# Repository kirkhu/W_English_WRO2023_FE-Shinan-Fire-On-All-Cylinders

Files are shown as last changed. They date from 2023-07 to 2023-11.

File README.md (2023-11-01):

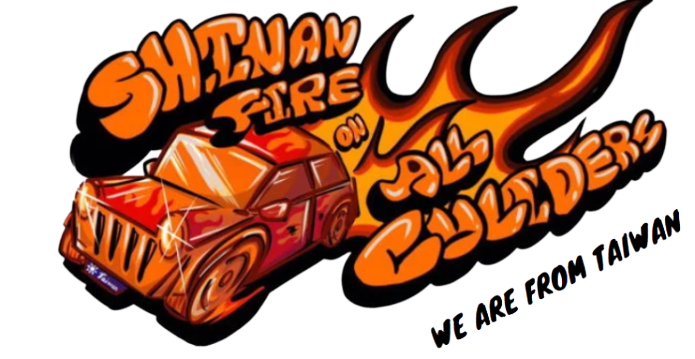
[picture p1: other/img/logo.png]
logo
 

- This is the official GitHub repository for the WRO TAIWAN team "__Shinan Fire On All Cylinders.__" All code, documentation, and files are located here.
- Here you can find the links to the technical report content and setup instructions, organized separately for learners and judges, for easy access during either learning or assessment. 
- In this technical document, the directory will be established based on the scoring criteria, and the directory headings will be hyperlinked for easy access for judges or learners to navigate to the key content of the technical document, facilitating quick assessment.  
    #### [For Learners](https://github.com/kirkhu/WRO2023_FE-Shinan-Fire-On-All-Cylinders/blob/main/learners_contents.md)
## Rubric for Judging Engineering Documentation 
- ###  ${{\color{red} Hardware Overview }} $ 
  #### 1. Mobility Management
    * [1-1 Vehicle 2D/3D Models in CAD](https://github.com/kirkhu/WRO2023_FE-Shinan-Fire-On-All-Cylinders/blob/main/models/Vehicle_2D_3D/README.md)
    * [1-2 Motor Selection](https://github.com/kirkhu/WRO2023_FE-Shinan-Fire-On-All-Cylinders/blob/main/schemes/Motor/README.md)
    * [1-3 Vehicle Chassis Design](https://github.com/kirkhu/WRO2023_FE-Shinan-Fire-On-All-Cylinders/blob/main/schemes/Vehicle_Chassis_Design/README.md)

  #### 2. Power and Sense Management
    - __Vehicle Design__
      - [2-1-1 BOM Parts List](https://github.com/kirkhu/WRO2023_FE-Shinan-Fire-On-All-Cylinders/blob/main/schemes/Parts_List#readme)
      - [2-1-2 Circuit Design](https://github.com/kirkhu/WRO2023_FE-Shinan-Fire-On-All-Cylinders/blob/main/models/Circuit_Design/README.md)
      - [2-1-3 Hardware Fool-Proof Design](https://github.com/kirkhu/WRO2023_FE-Shinan-Fire-On-All-Cylinders/blob/main/schemes/fool-proof-design/README.md) 
      - [2-1-4 Assembly Instructions & Wiring Diagrams](https://github.com/kirkhu/WRO2023_FE-Shinan-Fire-On-All-Cylinders/blob/main/schemes/Assembly_Instructions/README.md)    
      
    - __Power Management__
      - [2-2-1 Power Supply System](https://github.com/kirkhu/WRO2023_FE-Shinan-Fire-On-All-Cylinders/blob/main/schemes/Power_supply_system/README.md) 
      - [2-2-2 Li-Polymer Battery Low Voltage Alarm and Charging Equipment](https://github.com/kirkhu/WRO2023_FE-Shinan-Fire-On-All-Cylinders/blob/main/schemes/Li-Polymer_Battery/README.md)  
   
    - __Controller Selection__
      - [2-3-1 Controller Comparison](https://github.com/kirkhu/WRO2023_FE-Shinan-Fire-On-All-Cylinders/tree/main/other/Controller_Choosing)
    - __Sense Management__
      - [2-4-1 Color Sensor Introduction](https://github.com/kirkhu/WRO2023_FE-Shinan-Fire-On-All-Cylinders/blob/main/schemes/color_sensor/README.md)
      - [2-4-2 Lidar Selection](https://github.com/kirkhu/WRO2023_FE-Shinan-Fire-On-All-Cylinders/blob/main/schemes/Lidar/README.md)
      - [2-4-3 Camera Selection](https://github.com/kirkhu/WRO2023_FE-Shinan-Fire-On-All-Cylinders/blob/main/schemes/Camera/README.md)
  
- ### ${{\color{red} Software Overview }} $ 
  #### 3. Obstacle Management
    - [3-1 OpenCV Introduction](https://github.com/kirkhu/WRO2023_FE-Shinan-Fire-On-All-Cylinders/blob/main/other/OpenCV/README.md)
    - [3-2 ROS Introduction](https://github.com/kirkhu/WRO2023_FE-Shinan-Fire-On-All-Cylinders/blob/main/other/ROS)
    - [3-3 Software Platform Construction](https://github.com/kirkhu/WRO2023_FE-Shinan-Fire-On-All-Cylinders/blob/main/src/System_Platform_Software/README.md)
    - __Image Processing and Steering__
      - [3-4-1 Image Processing](https://github.com/kirkhu/WRO2023_FE-Shinan-Fire-On-All-Cylinders/blob/main/src/Image_Processing_and_Steering/Image_Processing/README.md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)  
      - [3-4-2 Steering Overview](https://github.com/kirkhu/WRO2023_FE-Shinan-Fire-On-All-Cylinders/blob/main/src/Image_Processing_and_Steering/Steering_overview/README.md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) 
    - __Programming__
      - [3-5-1 Open Challenge Code Overview](https://github.com/kirkhu/WRO2023_FE-Shinan-Fire-On-All-Cylinders/blob/main/src/Programming/Open_Challenge)
      - [3-5-2 Obstacle Challenge Code Overview](https://github.com/kirkhu/WRO2023_FE-Shinan-Fire-On-All-Cylinders/blob/main/src/Programming/Obstacle_Challenge)
      - [3-5-3 Distinctive Pseudo Code](https://github.com/kirkhu/WRO2023_FE-Shinan-Fire-On-All-Cylinders/blob/main/src/Distinctive_Pseudo_Code/README.md)
- ### ${{\color{red} Other}} $
  #### 4. Pictures – Team and Vehicle
    - [4-1 Team Members Introduction](https://github.com/kirkhu/WRO2023_FE-Shinan-Fire-On-All-Cylinders/blob/main/t-photos/README.md) 
    - [4-2 Vehicle Photos](https://github.com/kirkhu/WRO2023_FE-Shinan-Fire-On-All-Cylinders/tree/main/v-photos)  
  #### 5. Performance Videos
    - [5-1 Open Challenge](https://github.com/kirkhu/WRO2023_FE-Shinan-Fire-On-All-Cylinders/blob/main/video/Open_Challenge/video.md)
    - [5-2 Obstacle Challenge](https://github.com/kirkhu/WRO2023_FE-Shinan-Fire-On-All-Cylinders/blob/main/video/Obstacle_Challenge/video.md)
    - [5-3 Self-Driving Car Design Process Video](https://github.com/kirkhu/WRO2023_FE-Shinan-Fire-On-All-Cylinders/blob/main/video/ALL_video/video.md)
  #### 6. GitHub Utilization
    - [6-1 GitHub Edit(VScode Edit/GIT)](https://github.com/kirkhu/WRO2023_FE-Shinan-Fire-On-All-Cylinders/blob/main/src/GitHub_Edit/README.md)
    - [6-2 GitHub Web Editing Languages](https://github.com/kirkhu/WRO2023_FE-Shinan-Fire-On-All-Cylinders/blob/main/src/GitHub_Languages/README.md)  
  #### 7. Engineering Factor  
    - [7-1 Work Diary](https://github.com/kirkhu/WRO2023_FE-Shinan-Fire-On-All-Cylinders/blob/main/other/work_diary/README.md)
- ### ${{\color{red} CompetitionSchedule}} $  
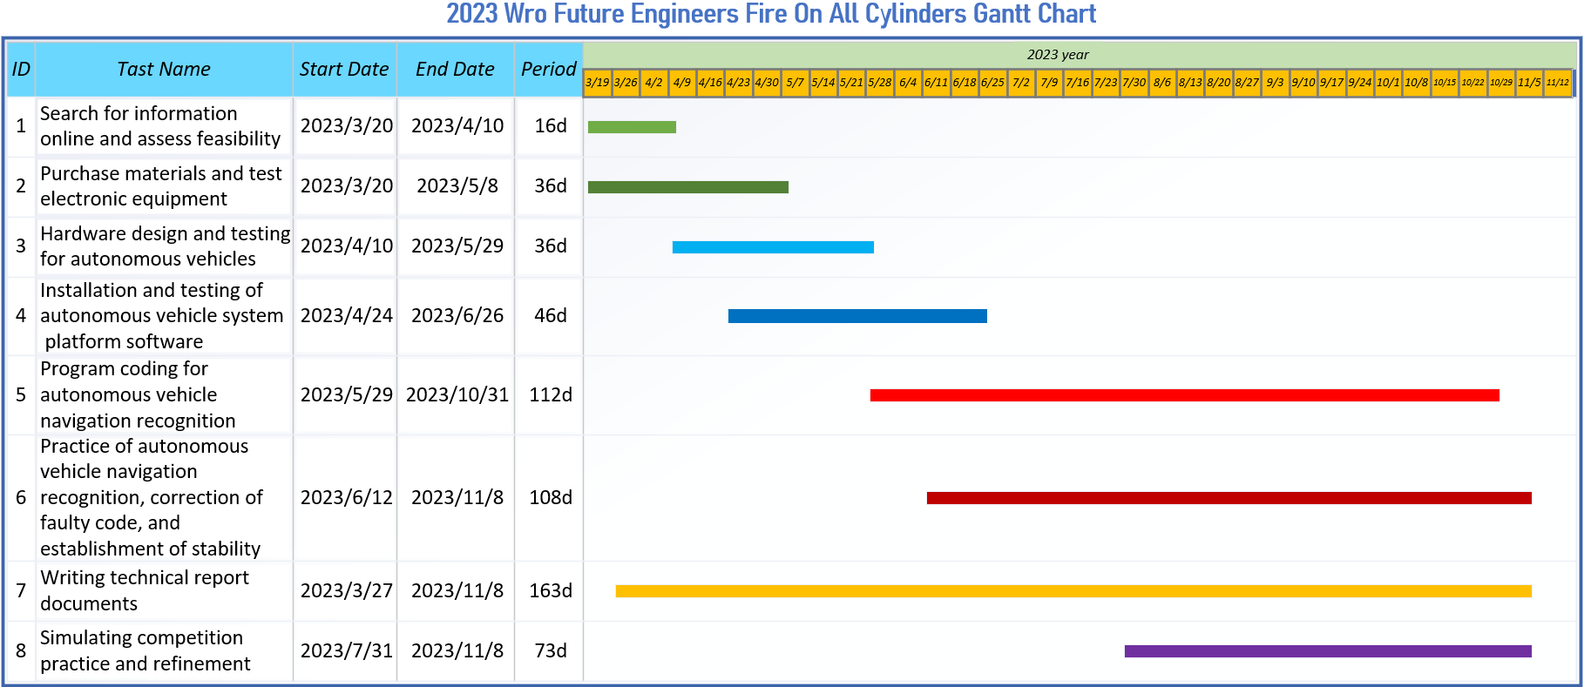
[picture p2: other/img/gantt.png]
Competition Schedule Gantt
#

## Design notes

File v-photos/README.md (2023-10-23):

<div align="center">logo</div>

- ## Vehicle's photos
<div align="center">
<table>
  <tr align="center">
    <th>Top view</th>
    <th>Bottom view </th>

  </tr>
    <tr align="center">
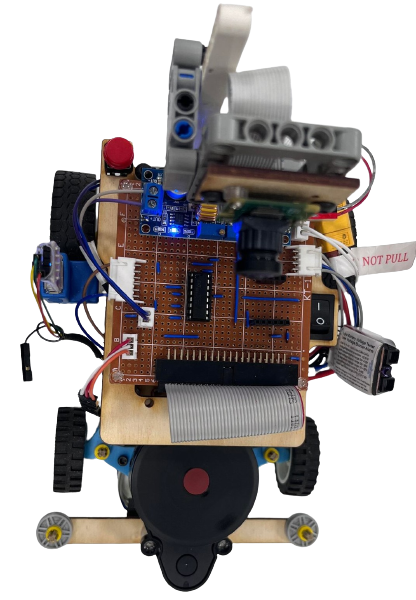
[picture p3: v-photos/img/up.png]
Top view
    <td> </td>
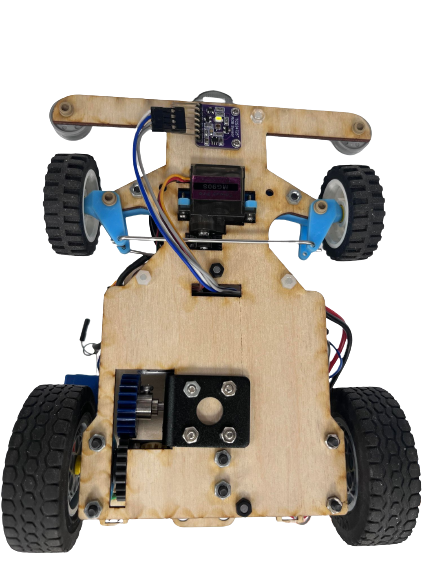
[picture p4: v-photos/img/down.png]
Bottom view
    <td></td>
  </tr>
    <tr align="center">
    <th> Front view</th>
    <th> Rear view </th>
  </tr>
    </tr>
    <tr align="center">
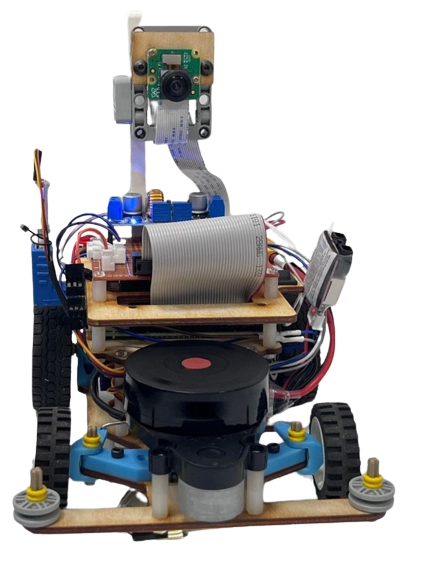
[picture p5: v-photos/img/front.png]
Front_view
    <td></td>
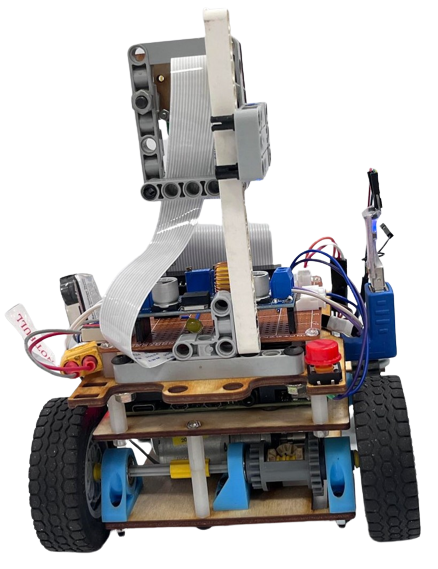
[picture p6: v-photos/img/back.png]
Rear_view
    <td></td>
  </tr>
    <tr align="center">
    <th> Left view</th>
    <th> Right view</th>
  </tr>
    </tr>
    <tr align="center">
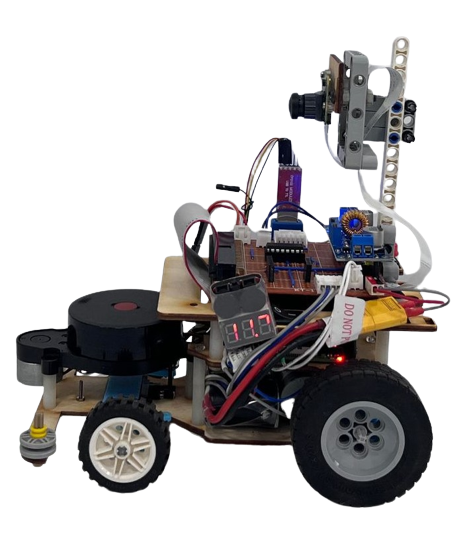
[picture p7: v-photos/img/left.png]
Left_view
    <td></td>
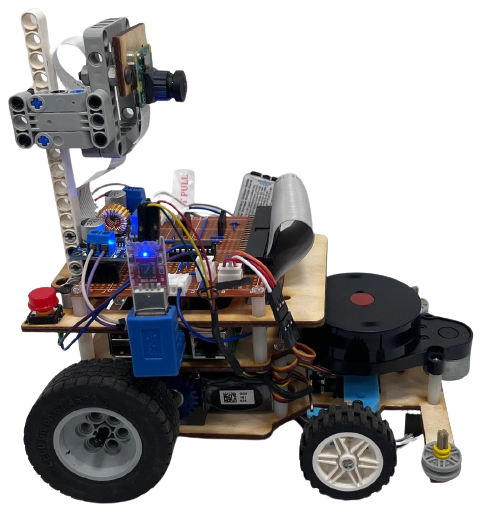
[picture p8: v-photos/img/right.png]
Right_view
    <td></td>
  </tr>
</table>
</div> 

- ## Mechanical Structure 
<div align="center">
<table>
  <tr align="center">
      <th>Overall Mechanical Structure Top View</th>
      <th>Middle-Level Mechanical Structure Top View</th>
      <th>Vehicle Chassis Top Views</th>
      <th>Vehicle Chassis Bottom View</th>
  </tr>
  <tr align="center">
     <td>Overall Mechanical Structure Top View      </td>
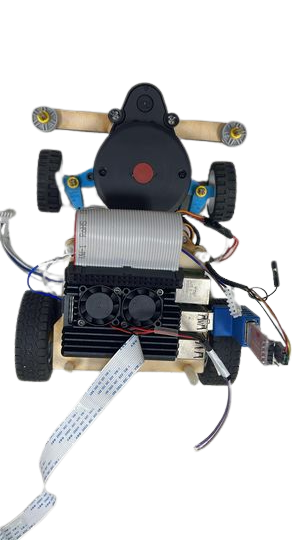
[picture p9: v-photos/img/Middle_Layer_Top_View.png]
Middle-Level Mechanical Structure Top View
     <td></td>
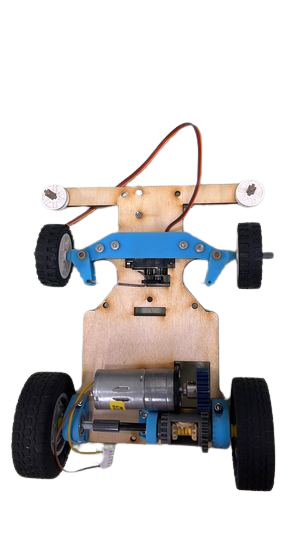
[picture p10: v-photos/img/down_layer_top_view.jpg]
Vehicle Chassis Top View
     <td></td>
     <td>BVehicle Chassis Bottom View</td>
  </tr>
</table>
</div>

- ### Circuit Board
<div align="center">
<table>
  <tr align="center">
      <th>Circuit Board of Top View</th>
      <th>Circuit Board of Bottom View</th>
  </tr>
  <tr align="center">
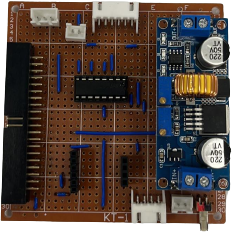
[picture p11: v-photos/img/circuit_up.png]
     <td>  </td>
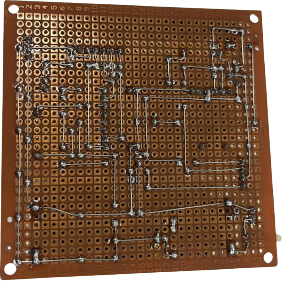
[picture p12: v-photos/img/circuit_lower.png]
     <td></td>
  </tr>
</table>
</div>

# <div align="center">HOME[Return Home](../)</div>

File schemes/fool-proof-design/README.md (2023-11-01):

<div align="center">logo</div>

## <div align="center">Hardware Fool-Proof Design</div>

- In the process of hardware design, there have been several cases of damage to Raspberry Pi controllers or ICs due to incorrect power connections or data cable insertion. To avoid this problem, we adopted a solution of using male and female sockets for power supply and data transmission. Through male and female sockets, the correct wiring is ensured, effectively avoiding the risk of Raspberry Pi or IC burning. This design improvement has increased the stability of the hardware system, improved the overall reliability and service life of the product.  
- In the process of hardware design, we initially used breadboards to connect circuits, but unfortunately encountered some cases of burning or poor contact, which led to abnormal function operation or potential problems that were difficult to find. To improve this situation, we decided to use soldering to fix the circuit on a PCB. This change has significantly reduced the risk of burning or poor contact, while ensuring a stable and reliable connection. Through this improvement, we have successfully improved the overall reliability of the hardware system and ensured the normal operation of the function.

<div align="center">

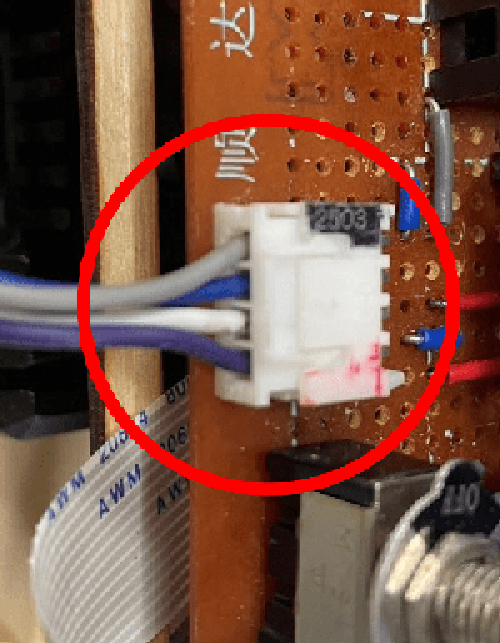
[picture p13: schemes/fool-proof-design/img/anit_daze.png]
Socket
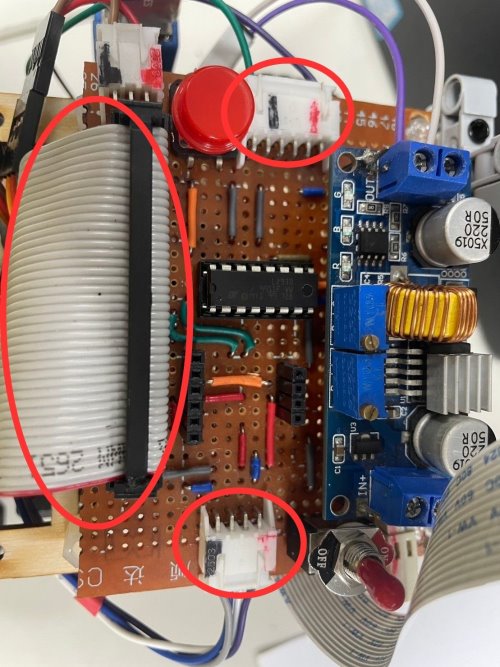
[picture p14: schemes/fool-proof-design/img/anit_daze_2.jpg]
Circuit Board
|   | |
|:----|:----:|
</div>
  
# <div align="center">HOME[Return Home](../../)</div>

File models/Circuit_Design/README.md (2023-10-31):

<div align="center">logo</div>

## <div align="center">Circuit Design </div>

 - In the design of self-driving car circuits, we used the Fritzing circuit software to draw circuit diagrams according to the functions required by self-driving cars. This method allows construction workers to follow the drawings and reduce errors.
 - The circuit board for the self-driving car is not a finished product that we purchased. Instead, we soldered it ourselves using a phenolic universal board, according to the circuit diagram we designed in advance.
 - Power and signal are two essential parts of self-driving car circuits. Power provides electricity to the circuit, while signal transmits data. Designing socket methods around the circuit board can facilitate the connection of sensors or batteries, which can improve the flexibility and scalability of the circuit.
   
 - #### Circuit Board
<div align="center">
<table>
  <tr align="center">
      <th> Circuit Board Top View</th><th>Circuit Board Button View</th>
  </tr>
  <tr align="center">
     <td> circuit_up </td><td></td>
  </tr>
</table>
</div>

- ### Circuit Schematic Drawing
<div align="center">
<table>
  <tr align="center">
      <th>Circuit Diagram</th><th>PCB Layouts</th><th>Circuit Schematic</th>
  </tr>
  <tr align="center">
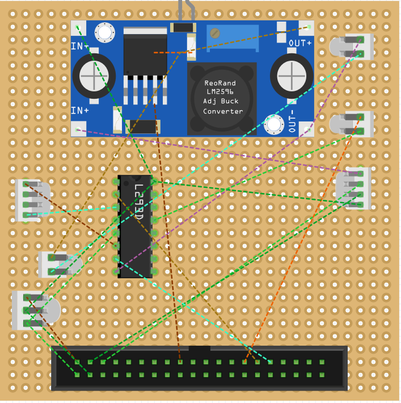
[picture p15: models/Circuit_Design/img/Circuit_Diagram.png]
Circuit Diagram
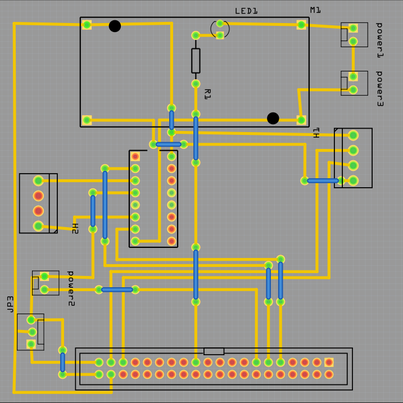
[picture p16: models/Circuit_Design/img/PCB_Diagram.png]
PCB Layouts
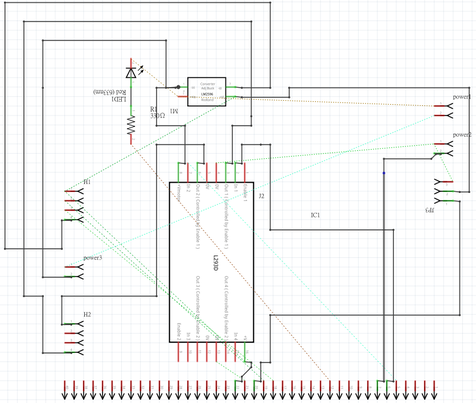
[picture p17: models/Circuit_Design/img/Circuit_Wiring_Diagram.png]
Circuit Schematic
     <td></td><td></td><td></td>
  </tr>
</table>
</div>

- ### Fritzing Introduction
  - Fritzing is a free and open-source electronic design automation (EDA) software. It provides a graphical user interface (GUI) for designing electronic circuits and circuit boards. Fritzing also includes a breadboard simulator, which allows users to test their circuits before building them.  
  - Fritzing is a popular choice for hobbyists and beginners, as it is easy to use and does not require any prior knowledge of electronics. It is also used by professional engineers for prototyping and designing electronic circuits.
  - Fritzing has a number of features that make it a powerful tool for electronic design, including:  
    - A large library of electronic components, including resistors, capacitors, transistors, and integrated circuits (ICs).  
    - A breadboard simulator that allows users to test circuits before building them.  
    - A PCB (printed circuit board) designer that allows users to create custom circuit boards.   
    - A schematic editor that allows users to create circuit diagrams.
  - In general, Fritzing is a very useful tool for a variety of electronic design applications. It is a good choice for hobbyists and beginners because it is easy to use and powerful. It is also a good choice for professional engineers because it has a wide range of features.
  - The circuit diagrams created for this competition are all designed using Fritzing.
  - Software link：[Fritzing](https://fritzing.org/)  
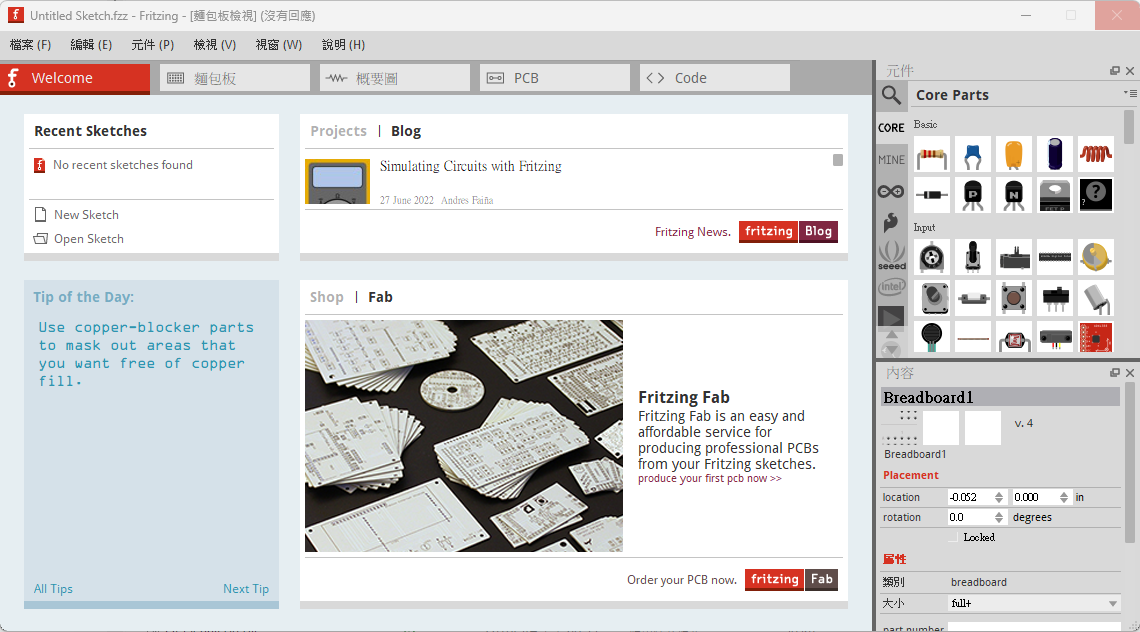
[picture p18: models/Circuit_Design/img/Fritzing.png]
Fritzing
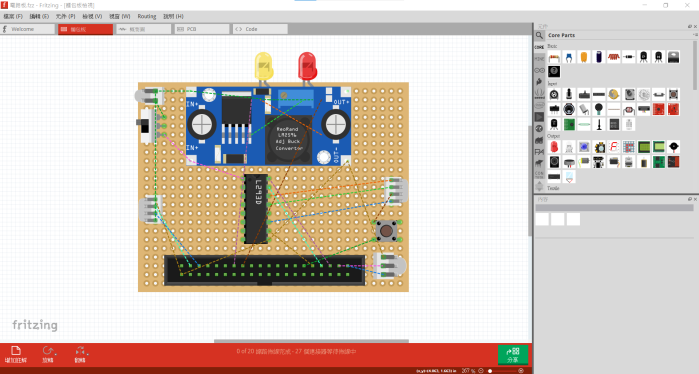
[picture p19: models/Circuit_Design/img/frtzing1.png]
  

# <div align="center">HOME[Return Home](../../)</div>

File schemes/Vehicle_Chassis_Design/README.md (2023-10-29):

<div align="center">logo</div>

## <div align="center">Vehicle Chassis Design Process</div> 

- ### Vehicle Chassis Design
  - The vehicle chassis used in this competition is self-designed and developed.
  - We applied Ackermann Steering Geometry to the vehicle chassis mechanism to facilitate obstacle avoidance and U-turns.
  - The following table shows the 3D models and finished products of the vehicle chassis.

    |3D Vehicle Chassis Design| Vehicle Chassis Top View | Vehicle Chassis Bottom View|
    |:----:|:----:|:----:|
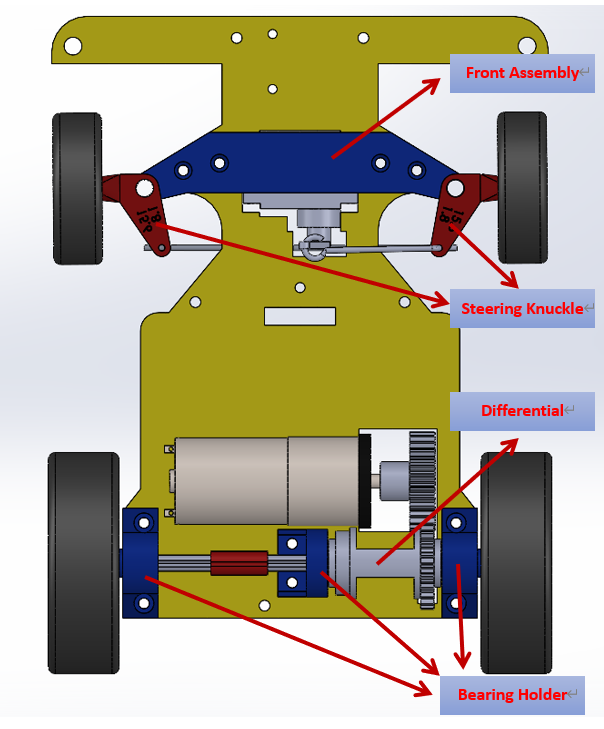
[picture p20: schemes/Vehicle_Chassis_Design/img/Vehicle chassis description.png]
vehicle_chassis_design_3D
    ||up_view|down_view|

    - We used a Stereolithography (SLA) 3D Printer and laser -cutting machine to design and produce all the components on the vehicle chassis, except for the gears, differential, and tires. This approach not only saves space but also allows us to customize dimensions and shapes according to the specific needs of the vehicle.
    - By incorporating bearings into the vehicle's support frame, we've reduced friction, thereby increasing the vehicle's speed.
    - The support frame for the Ackermann steering geometry on the vehicle chassis was designed through 3D modeling, and the model was then produced using a stereolithography (SLA) 3D printer. This approach allows for the flexible adjustment of the Ackermann ratio, helping us determine the optimal turning radius with precision.

- #### Vehicle Chassis Improvement Record

    - In the process of designing the vehicle chassis, we encountered many issues. We will document the problem-solving and modification process in the following table:

        |First Prototype | Explanation |
        |:----:|:----|
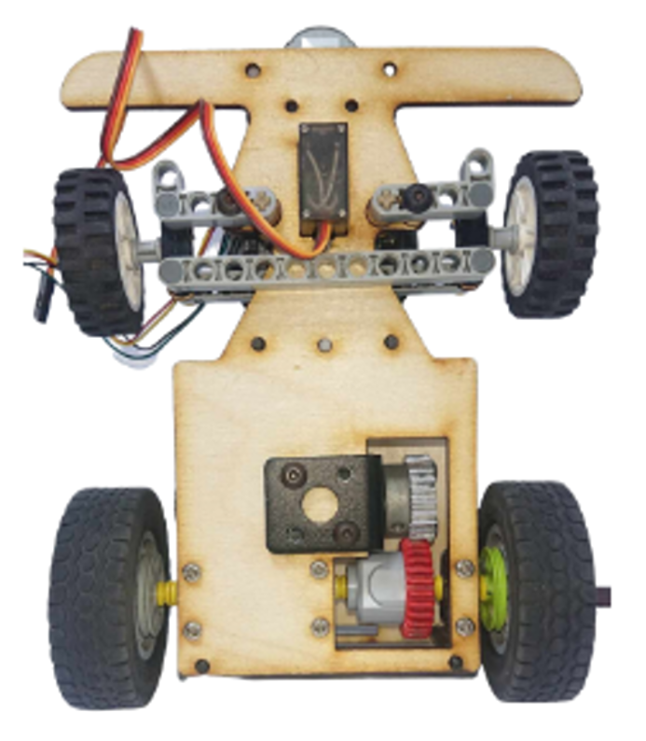
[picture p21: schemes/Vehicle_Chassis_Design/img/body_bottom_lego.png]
body_bottom_lego
        ||This is the first prototype of the chassis assembled using LEGO and wooden boards. However, during assembly, many structural components couldn't be realized due to the constraints of LEGO specifications, such as the Ackermann steering mechanism.|

        |Second Prototype| Explanation|
        |:----:|:----|
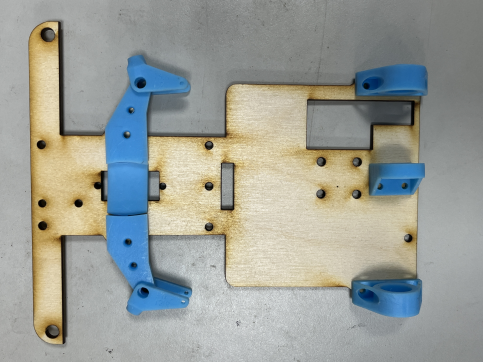
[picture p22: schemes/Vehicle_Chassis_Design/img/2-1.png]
        ||To ensure smoother wheel rotation, we incorporated bearings. We utilized a Stereolithography (SLA) 3D Printer to create the bearing mounts, which were then accurately aligned with corresponding holes cut into the wooden board.|

        |Third Prototype | Explanation|
        |:----:|:----|
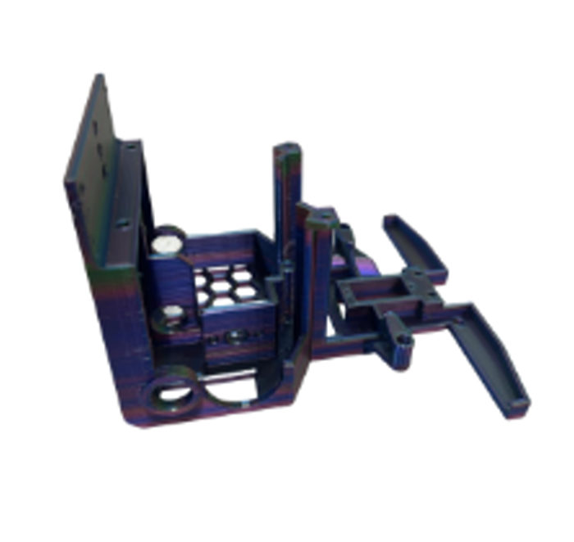
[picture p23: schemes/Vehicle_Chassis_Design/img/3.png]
        || We attempted to create an integrated chassis structure through 3D printing. The advantage we considered was that it eliminates the need to assemble it in separate parts, making the model more compact. However, later we discovered that the 3D printed base was quite fragile and prone to breaking.|

        |Fourth Prototype | Explanation|
        |:----:|:----|
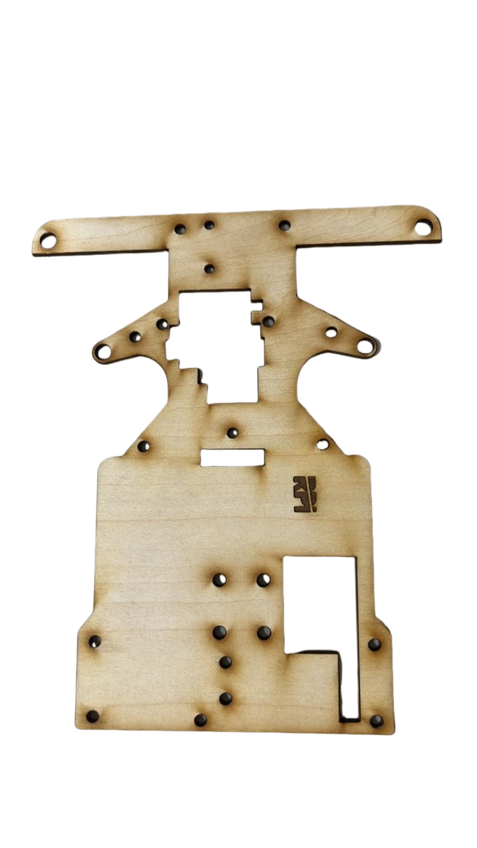
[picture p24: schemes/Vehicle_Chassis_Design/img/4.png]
        ||Due to the fragility of the 3D printed material, we reverted back to using the original wooden board material. Additionally, we adjusted the placement of the servo motor to lower its position, thus reducing the center of gravity and enhancing stability.|

        |Final Build | Explanation|
        |:----:|:----|
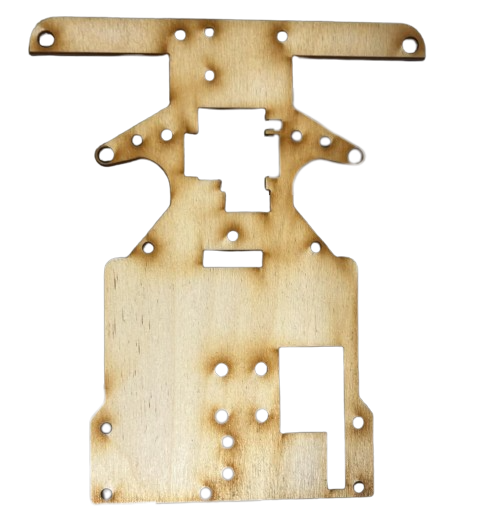
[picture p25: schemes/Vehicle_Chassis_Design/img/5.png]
        ||The key change in this edition is shifting the position of the servo motor from being on the left side to being in the center. Otherwise, the left wooden board would be too thin and prone to breaking.|

- #### What is an Ackermann Steering Geometry?

  - #### Ackermann Steering Geometry Introduction 
    - The Ackermann steering geometry, proposed by German automotive engineer Lankensperger in 1817, is a steering system design used in automobiles. It was developed to address the geometric discrepancy in the paths of the inner and outer turning wheels when a vehicle makes a turn.
    - People apply Ackermann steering geometry to the steering mechanism of vehicles. Through the corresponding cranks of the four-linkage system, the steering angle of the wheels relative to the projected tire is increased by about 2 to 4 degrees. This results in the rough convergence of the trajectory centers of all four wheels along the extension line of the rear axle, thereby achieving the vehicle's turning.
      
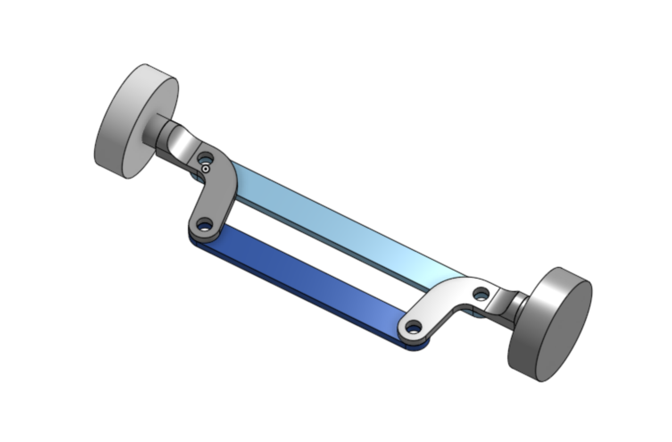
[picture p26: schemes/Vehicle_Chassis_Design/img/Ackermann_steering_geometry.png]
Ackermann_steering_geometry
        

      Reference Link：[Ackermann steering geometry@Wikipedia](https://zh.wikipedia.org/zh-tw/%E9%98%BF%E5%85%8B%E6%9B%BC%E8%BD%89%E5%90%91%E5%B9%BE%E4%BD%95)
      #### The principle of Ackermann steering geometry is based on the following concepts:     
       - __Difference in Turning Radius:__ When the vehicle makes a turn, the two front wheels need to rotate at different angles to allow the vehicle to pivot around a central point.
       - __Turning Angles of the Two Front Wheels:__ The design of the Ackermann steering geometry ensures that both front wheels pass through a central point simultaneously during steering.
    - Compared to the Ackermann steering geometry made from the original 0% LEGO bricks, the steering mechanism of this competition vehicle is designed with reference to an 80% Ackermann steering geometry. It offers advantages such as reduced resistance and smoother turns. The Ackermann steering geometry parts are produced using a stereolithography (SLA) 3D printer. However, the most challenging aspect of the process was adjusting the Ackermann ratio to achieve the ideal turning angle for our vehicle to navigate around blocks effectively.  
  
  - #### Why Choose an 80% Ackermann Ratio?

    - In theory, this design is the optimal choice for smooth and efficient turns. However, it may lead to excessive tire wear. Therefore, in automobile design, a 100% Ackermann ratio is usually not chosen. Compared to a 100% Ackermann ratio, an 80% Ackermann ratio allows for smoother, more predictable turns, improves maneuverability, and reduces tire wear.

  - #### Producing Ackermann steering geometry components (80% Ackermann angle) using Stereolithography (SLA) 3D Printer
    - The Ackermann steering geometry components within the red box in the bottom-left diagram are assembled using LEGO bricks.
    - The Ackermann steering geometry components within the red box in the bottom-right diagram are assembled from self-produced plastic parts using a Stereolithography (SLA) 3D Printer.
    - Assembling the steering system with LEGO bricks can save costs and time, while using a Stereolithography (SLA) 3D printer to manufacture plastic parts can enhance precision and customization.
    - During the process of production and testing, we found that using LEGO bricks was limited by the original specifications, making it difficult to create a structure that perfectly suited our needs. In contrast, utilizing a Stereolithography (SLA) 3D Printer to produce the Ackermann steering geometry components allowed for customization in size and shape, giving us the flexibility to design and print according to our specific requirements. 
    - __As a result, we ultimately decided to use the SLA 3D Printer to manufacture the Ackermann steering geometry components for the vehicle's steering mechanism.__

    <div align=center>
    <table>
    <tr>
    <th>Assembling with LEGO Bricks.</th>
    <th>Assembled Using Photocured PartsAssembling Parts Produced with a SLA 3D Printer</th>
    </tr><tr>
    <td></td>
    <td align=center></td>
    </tr>
    </table>
    </div>

    - #### Calculating the Ackermann Angle Graphically (a-b = ack)

    <div align="center">
    <table>
    <tr align=center>
    <td>angle</td>
    <td>Ackermann_steering_geometry_lego</td>
    </tr>
    </table>
    </div>

    Reference Video website：[汽车转弯 没那么简单: 阿克曼转向几何是个啥？How does Ackerman steering geometry work?](https://www.youtube.com/watch?v=8AimxDPWKcM)

- ###  Gear Differential

  - The gear differential is a crucial component of a vehicle's drivetrain, used to balance and distribute power to different wheels.
  - It allows the driven wheels to rotate at different speeds, especially during turns. This is crucial for enhancing the vehicle's agility and maneuverability. The gear differential achieves this function through a series of gear mechanisms, enabling the two drive wheels to rotate adaptively, ensuring the stability and balance of the vehicle, and maintaining good driving conditions regardless of road conditions.
   - #### The LEGO Brick Gear Differential Introduction 
        - In this competition, we use a LEGO brick gear differential to achieve the function of the vehicle driving and turning.
        - There are two types of LEGO brick gear differentials: LEGO 65414 Differential Gear and LEGO 6573 Differential Gear.
        - LEGO 65414 Differential Gear: It consists of the 28-tooth gear from LEGO 65413 and five LEGO Gear 12 Tooth Bevel 4565452.
        - LEGO 6573 Differential Gear: Integrating a 16-tooth gear and a 24-tooth gear, both gears have a 5mm diameter hole in the center for easy placement of a cross axle. There is a small pillar in the center of the differential, allowing us to better secure the right-angle bevel gears and combine three LEGO Gear 12 Tooth Bevel 4565452.

          <div align=center>
          <table>
          <tr align=center>
          <th>LEGO 65414 GearDifferential</th>
          <th>LEGO 6573 Gear Differential</th>
          </tr><tr align=center>
          <td></td>
          <td></td>
          </tr>
          </table>
          </div>

    - #### Reason for Selection
        - We originally used the LEGO 65414 gear differential as a steering system component. However, during testing, we found that the gear differential would occasionally disengage while the vehicle was driving, causing the vehicle to malfunction. As a result, we switched to the LEGO 6573 gear differential, which solved the problem.

        <div align="center">
        <table>
        <tr>
        <th>LEGO 65414 Gear Differential </th>
        <th>LEGO 6573 Gear Differential </th>
        </tr><tr align=center>
        <td></td>
        <td></td>
        </tr>
        </table>
        </div>

- ###  Vehicle Suspension and Shock Absorption System
    - We once attempted to address the issue of unstable weight distribution during vehicle turns by experimenting with a suspension system. Here is the description of our attempt.
    - Therefore, we chose the MacPherson strut system as the vehicle's suspension system, as it offers many advantages over the double-wishbone suspension system. The MacPherson strut system is characterized by its simple structure, ease of manufacturing, and space efficiency. Additionally, the MacPherson strut system is widely used in modern vehicles, especially in the front-wheel suspension system.
    - The main components of the system include:  
      - Spring: Typically composed of a spring and a shock absorber, it connects the wheel to the chassis, absorbing vibrations and impacts from uneven road surfaces.
      - Upper control arm: Located above the wheel, it connects the chassis to the wheel. Its design allows the wheel to move freely in the vertical direction.
      - Lower control arm: Connects the chassis to the wheel and helps control the motion of the wheel.
    - We designed two options. The first option had a larger vertical vibration range both above and below, which couldn't effectively control the vehicle's vibration. Therefore, we chose the second option, which had a smaller vibration amplitude and could also maintain a lower center of gravity for the vehicle.

        <div align="center">
        <table>
            <tr align="center">
            <th>Big Range</th>
            <th>Small Range</th>
            <th>Actual Application Image</th>
            </tr>
            <tr align="center">
            <td>big range</td>
            <td>small range</td>
            <td></td>
            </tr>
        </table>  
        </div> 

      Due to the smoothness of the competition venue, the shock absorbers cannot provide significant damping effect. __Therefore, we have decided to omit the use of shock absorbers to reduce the complexity in vehicle fabrication.__

# <div align="center">HOME[Return Home](../../)</div>

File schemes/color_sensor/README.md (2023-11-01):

<div align="center">logo</div>

# <div align="center">Color Sensor Introduction</div> 
 __Color Sensor-TCS34725__
<div align="center">
<table>
<tr>  
<td>
<ul>
  <li>The TCS34725 color sensor has been chosen because it meets all the requirements of this competition. Firstly, it possesses outstanding sensing capabilities, allowing it to quickly and accurately identify the colors of the ground lines. Secondly, the sensor is thin and compact, enabling it to be placed close to the ground without interfering with the vehicle's movements.</li>
  <li>The TCS34725 color sensor has two primary functions on the vehicle:</li>
  <ol>
  <li>It can count laps around the track by detecting the blue and orange lines on the field.</li>
  <li>By detecting the sequence of blue and orange lines through the color sensor, it can determine whether the vehicle is currently moving in a clockwise or counterclockwise direction. This information is used by the program to calculate the number of clockwise and counterclockwise turns, ensuring that the vehicle can smoothly return to the starting area after completing 3 laps.</li>
  </ol>
</ul>
</td>
 <td width=250 >TCS34725 
</td>
</tr>
</table> 
</div>
  
We encountered a bottleneck when using the color sensor to detect lines because we was unsure how to write a Python program to detect the values of blue and orange lines. 
        
With the guidance of my teacher, We successfully completed it.  
 __The partial code is as follows:__
  #### Function
```
class TCS34725():
    def __init__(self):
        self.enable_selection()
        self.time_selection()
        self.gain_selection()
    def enable_selection(self):
        """Select the ENABLE register configuration from the given provided values"""
        ENABLE_CONFIGURATION = (TCS34725_REG_ENABLE_AEN | TCS34725_REG_ENABLE_PON)
        bus.write_byte_data(TCS34725_DEFAULT_ADDRESS, TCS34725_REG_ENABLE | TCS34725_COMMAND_BIT, ENABLE_CONFIGURATION)
    def time_selection(self):
        """Select the ATIME register configuration from the given provided values"""
        bus.write_byte_data(TCS34725_DEFAULT_ADDRESS, TCS34725_REG_ATIME | TCS34725_COMMAND_BIT, TCS34725_REG_ATIME_2_4)
        """Select the WTIME register configuration from the given provided values"""
        bus.write_byte_data(TCS34725_DEFAULT_ADDRESS, TCS34725_REG_WTIME | TCS34725_COMMAND_BIT, TCS34725_REG_WTIME_2_4)
    def gain_selection(self):
        """Select the gain register configuration from the given provided values"""
        bus.write_byte_data(TCS34725_DEFAULT_ADDRESS, TCS34725_REG_CONTROL | TCS34725_COMMAND_BIT, TCS34725_REG_CONTROL_AGAIN_1)
    def readluminance(self):
        """Read data back from TCS34725_REG_CDATAL(0x94), 8 bytes, with TCS34725_COMMAND_BIT, (0x80)
        cData LSB, cData MSB, Red LSB, Red MSB, Green LSB, Green MSB, Blue LSB, Blue MSB"""
        data = bus.read_i2c_block_data(TCS34725_DEFAULT_ADDRESS, TCS34725_REG_CDATAL | TCS34725_COMMAND_BIT, 8 )        
  # Convert the data
        cData = data[1] * 256 + data[0]
        red = data[3] * 256 + data[2]
        green = data[5] * 256 + data[4]
        blue = data[7] * 256 + data[6]        
  # Calculate luminance
        luminance = (-0.32466 * red) + (1.57837 * green) + (-0.73191 * blue)
        return {'c' : cData, 'r' : red, 'g' : green, 'b' : blue, 'l' : luminance}
``` 
  #### Snippet of Code  
```
data = bus.read_i2c_block_data(TCS34725_DEFAULT_ADDRESS, TCS34725_REG_CDATAL | TCS34725_COMMAND_BIT, 8 )        
        # Convert the data
        cData = data[1] * 256 + data[0]
        red = data[3] * 256 + data[2]
        green = data[5] * 256 + data[4]
        blue = data[7] * 256 + data[6]        
# Calculate luminance
        luminance = (-0.32466 * red) + (1.57837 * green) + (-0.73191 * blue)
        return {'c' : cData, 'r' : red, 'g' : green, 'b' : blue, 'l' : luminance}
```
- #### Algorithm for Detecting Blue and Orange Lines Using a Color Sensor
  1. After the program is started, it will first read the three original values of the field lines: blue (blue_color = 15), orange (orange_color = 27), and white (white_color = 35).
  2. Then, the light sensor will read the current color value of the field and record it in the variable color_value. If the detected color value is greater than white (35), the vehicle can move forward directly. Otherwise, it indicates that it may be one of the blue (15) or orange (27) lines.
  3. Next, the program will add the color values of blue (15) and orange (27) and then divide them by 2 to obtain the middle value of the color value.
  4. Finally, the program will use the value of color_value to determine which line it is. If color_value is lower than the middle value, it indicates that it is a blue line (15); if color_value is higher than the middle value, it indicates that it is an orange line (27). When the blue and orange lines are known first, the vehicle can be determined to go clockwise or counterclockwise.
  

# <div align="center">HOME[Return Home](../../)</div>

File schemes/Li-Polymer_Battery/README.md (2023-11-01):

<div align="center">logo</div>

## <div align="center">Li-Polymer Battery Low Voltage Alarm and Charging Equipment</div> 
 - #### Low Voltage Alarm
   Li-Polymer Battery Low Voltage Alarm
   <div align="center">
   <table>
   <tr>
   <td>The primary purpose of installing a low voltage alarm is to prevent the battery from reaching a critically low voltage, thereby avoiding abnormal vehicle operation or battery damage. Therefore, when the battery voltage drops below a specific threshold, the low voltage alarm will sound an alert, reminding the user to take notice or promptly replace the battery to prevent any disruptions to the ongoing race.  
        
   </td>
   <td>low_voltage_alarm</td>
    </tr>
   </table>
   </div>
   
  - #### Battery Charging/Discharging Equipment 
    - In general, rechargeable batteries, such as nickel-metal hydride (NiMH) and nickel-cadmium (NiCd) batteries, can be stored directly for long periods of time without any problem. However, Li-Polymer batteries should not be stored directly for long periods of time. If they are, the internal charge will gradually decrease, which can lead to a loss of capacity and even the inability to use the battery.
    - The long-term storage method for Li-Polymer batteries is as follows:
      1. Charge the battery to around 50% of its capacity.
      2. Use a charge/discharge device to discharge the battery to approximately 3.2V.
      3. Store the battery in a cool, dry place.  
            This approach can help extend the lifespan of lithium polymer batteries.
    - The following are the reasons for the deterioration of lithium polymer batteries when left unused for an extended period:
      1. Insufficient internal battery charge, leading to the inability of chemical reactions within the battery to proceed normally, resulting in a loss of battery capacity.
      2. Excessive internal battery charge, causing the breakdown of the battery's electrolyte and, in turn, damaging the battery.
      3. Storing the battery in a high-temperature or high-humidity environment, accelerating the chemical reactions within the battery and causing damage to the battery.

      <div align="center">
      <table>
        <tr align="center">
        <th>Skyrc E430</th>
        <th>Skyrc Imax B6C2 v2</th>
        <th>HOTA D6 Pro</th>
        </tr>
        <tr>
        <td></td>
        <td></td>
        <td></td>      
        </tr>

</table>
</div>

# <div align="center">HOME[Return Home](../../)</div>

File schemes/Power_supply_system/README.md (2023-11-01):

<div align="center">logo</div>

# <div align="center">Vehicle Power Supply System Introduction</div> 
- ### Power Supply Operation System Overview Diagram


- ###  Physical Connection Diagram of Power Supply System 


- ### Power Supply System Operation Instruction
  Each type of device operates at its respective working voltage, as explained below:
  - Powered by a lithium-polymer battery, it provides 11.1V, simultaneously serving as the working voltage for the 12V-to-5V step-down power supply module and the L293D motor control chip to drive the 12V DC motors.
  - The step-down power supply module reduces 11.1V to 5V, supplying the working voltage to the 5V Raspberry Pi, 5V color sensor, 5V L293D motor controller, and 5V servo motors.
  - The Raspberry Pi, in turn, supplies 5V as the working voltage for the Lidar and camera module.  - 
- ###  Battery Selection
  - As the vehicle requires continuous movement, it was necessary to switch the power source to batteries. Considering that the motors require a voltage of 12V to operate, we chose a 12V battery with a current rating of 3A.
  - There are two common battery options: lithium-ion batteries (18650) and lithium-polymer batteries (3S). However, due to the heavier weight and larger size of 18650 batteries, we opted for the compact and lightweight lithium-polymer battery.
  - #### Battery Comparison

<div align="center" width=100%>
<table>
<tr align="center">
  <th> 18650 Lithium Batteries </th> <th>Li-Polymer 3S Battery 
  </th>
</tr>
<tr align="center">
  <td>
   </td>
  <td>
  lipo_battery
  </td>
</tr>
</table>
</div>

 - ### Step-Down Power Supply Module  Selection
    - The Raspberry Pi can only operate at a voltage of up to 5.2V, so we need to use a 12V-to-5V step-down power supply module to lower the voltage and prevent damage to the Raspberry Pi.
    - Initially, we used the LM2596 DC-DC adjustable step-down module because it had a digital display that could show the current output voltage. However, its maximum output current was only 3A, which couldn't meet the device's operating current, so we didn't use it.
    - Therefore, we opted for a constant voltage and constant current step-down power supply module with a maximum output current of 5A, which allows the self-driving car to operate normally. While it lacks a digital display, we can determine the current battery voltage through a low-voltage alarm, ensuring that the battery voltage is sufficient.
    - #### Step-Down Power Supply Module Comparison
<div align="center">
<table with=100%>
<tr align="center">
<th> LM2596 DC-DC Adjustable Buck Converter Module </th>
<th>5V Constant Voltage Constant Current Buck Power Supply Module</th>
</tr>
<tr align="center">
  <td>MG90S  </td>
  <td>MG90S 
  </td>
</tr>
</table>
</div>

# <div align="center">HOME[Return Home](../../)</div>

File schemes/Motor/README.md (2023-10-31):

<div align="center">logo</div>

# <div align="center"> Motor Selection</div> 
When the vehicle is in motion, the Raspberry Pi sends speed information to __the motor controller(L293D)__ to control the __rear-wheel drive DC motor__. Simultaneously, the Raspberry Pi also sends messages to the __servo motor of the front steering mechanism__, enabling the vehicle to maneuver freely and move forward.  

### Front Steering Mechanism by Servo Motor
- To select a servo motor among commonly available options in the market, considering factors such as weight, rotation angle, and torque, we have identified two suitable servo motors: MG90S and SG90.
- The difference between MG90S and SG90 lies in the front gears, where the former has metal gears, while the latter has plastic ones. Since we often require continuous rotation, we have __chosen the MG90S__ due to its durability, as it is less prone to damage.

<div align="center">
<table>
<tr ><th colspan="3">Servo Motor Comparison</th></tr>
<tr align="center">
<th rowspan="2" >Model</th>
<th>MG90S</th>
<th>SG90</th>
</tr>
<tr align="center">
<td>MG90S</td>
<td> SG90</td>
</tr>
<tr align="center">
<td>Rotation Angle</td>
<td>90° MAX</td>
<td>360° MAX</td>
</tr>
<tr align="center">
<td>Torque</td>
<td>2.0kg/cm</td>
<td>1.4 kg/cm</td>
</tr>
<tr align="center">
<td>Speed</td>
<td>0.11s</td>
<td>0.1S</td>
</tr>
</table>
</div>

### Rear-Drive DC Motor
- When selecting a DC motor among commonly available options in the market, considering factors such as weight, rotational speed, and torque, we have identified the following four suitable DC motors.
- Among them, the three types of motors, JGA25, have different model numbers but share a similar physical appearance, and their differences are as follows.
<div align="center"><table>
<tr ><th colspan="5">DC Motor Comparison</th></tr>
<tr align="center">
<th rowspan="2" >Model</th>
<th >JGA25 370</th>
<th >JGA25 370</th>
<th >JGA25 371</th>
<th >JGA16-050</th>
</tr>
<tr align="center">
<td >JGA25-370_1360RPM</td>
<td >JGA25-370_620RPM</td>
<td >JGA25-371M</td>
<td >JGA16-050</td>
</tr>
<tr align="center">
<td >Speed</td>
<td >1360rpm</td>
<td >620rpm</td>
<td >294rpm</td>
<td >220rpm</td>
</tr>
<tr align="center"><td>Torque</td><td>4.27kg.cm</td><td>9.15kg.cm</td><td>5.2kg.cm</td><td>1.15kgcm</td></tr><tr align="center">
<td>Power</td><td>5.4W</td><td>5.4W</td><td>4.2W</td><td>0.33W</td>
</tr>
</table>
</div>  

- After conducting experimental research, we found that choosing the high-speed 1630rpm JGA-370 motor resulted in lower torque, making it difficult for the vehicle to move effectively. On the other hand, opting for the high-torque JGA-371 motor led to an excessively low rotational speed, which did not meet the requirements for the vehicle's operation.
- __Therefore, based on these findings, we ultimately selected the 620rpm JGA-370 motor as the rear-wheel drive DC motor for the vehicle. This choice strikes a balance between rotational speed and torque, providing the necessary performance for the vehicle's propulsion.__  

### Motor Drive Controller
- When testing the operation of the motor, simply providing power does not effectively control the movement of the GA25-370 motor, making it impossible to adjust the speed. Therefore, we need to install a motor controller to regulate the speed of the DC gear motor. Currently, there are two options available in the market: the L293D chip and the L298N module. To reduce weight, we __chose the smaller L293D chip.__   
- __Its compact size allows us to install more sensors, thereby saving space, reducing weight, and increasing the maneuverability of the vehicle.__

<div align="center">
<table>
<tr><th colspan="3">Motor Control Comparison</th></tr>
<tr align="center" >
<th rowspan="2">Model</th>
<th>L293D</th>
<th>L298N</th>
</tr>
<tr align="center">
<td> l293d</td>
<td >l298n</td>
</tr>
<tr align="center">
<td>Occupied Area(mm)</td>
<td>29.5x8</td>
<td>43.5x43.5</td>
</tr>
<tr align="center">
<td>Output Voltage</td>
<td>4.5V to 36V</td>
<td>5V to 46V</td>
</tr>
<tr align="center">
<td>Rated Power </td>
<td>5W</td>
<td>10W</td>
</tr>
</table>
</div>

# <div align="center">HOME[Return Home](../../)</div>

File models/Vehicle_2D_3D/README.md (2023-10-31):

<div align="center">logo</div>

## <div align="center">3D Vehicle Model Design</div>

 - The vehicle chassis used in this competition is our in-house, self-developed design. The following will introduce the vehicle chassis design and production process.
 - We use Onshape to design the 3D model structure of the vehicle, and based on the chassis's characteristics, we manufacture the necessary vehicle parts using equipment such as laser cutting machines and 3D printers.
- ### Onshape Model Draft
    <div align=center>
    <table>
    <tr>
    <th>3D Vehicle Model </th>
    <th>Vehicle Underfloor</th>
    <th>Vehicle Mid-Deck</th>
    <th>Vehicle Top Deck</th>
    </tr><tr>
    <td>Vehicle_cad</td> 
    <td>vehicle Underfloor</td> 
    <td>Vehicle_Mid_deck</td> 
    <td>Vehicle_Top_Deck</td>
    </tr>
    </table>
    </div> 
    <div align=center>
    <table>
    <tr>
    <th>3D Vehicle Chassis Design</th>
    <th>3D Vehicle Chassis Models</th>
    </tr><tr>
     <td></td> 
    <td></td> 
    </tr>
    </table>
    </div> 

  - #### Onshape Introduction
    - We use Onshape to design 3D models of self-driving cars. Onshape is a free and easy-to-use web-based CAD software.
    - After creating a model in Onshape, you can output a 2D dimension drawing, which can then be sent to a laser-cutting machine for cutting or converted and sent to a 3D printer for output.
    - All 3D/2D vehicle models created for this competition were designed in OnShape.
    - Software Website：[On Shape](https://www.onshape.com/en/) 

        |Onshape| Vehicle_cad_obshape|
        |:---:|:---:| 

- ### The Production of Vehicle Chassis Panels Introduction - Using a laser-cutting machine
  - A laser-cutting machine is a device that utilizes a laser beam to cut materials. The laser beam has high energy density and can cut a variety of materials, including wood, metal, plastic, paper, and more, quickly and precisely.
  - We use the laser-Cutting machine provided by the school to produce the 'vehicle underfloor,' 'vehicle mid-deck,' and 'vehicle top deck' required for the vehicle chassis. We cut 3mm thick wooden boards according to the self-designed vehicle flat panel dimensions chart.  
  - We use lighter-weight wooden boards as the material for vehicle flat panels to reduce the vehicle's weight.  
  - Here is an introduction to the process of creating vehicle flat panels using a laser cutting machine.

    - ####  Operation of Laser-Cutting Machine
    <div align="center">car_board</div>

    - #### Vehicle Chassis Panels Dimensions Chart
        <div align=center>
        <table>
        <tr>
        <th>Lens Holder</th>
        <th>Vehicle Underfloor</th>
        <th>Vehicle Mid-Deck</th>
        <th>Vehicle Top Deck</th>
        </tr><tr>
        <td>lens_holder</td> 
        <td>2D_bottom</td> 
        <td>2D_mid</td> 
        <td>2D_top</td>
        </tr>
        </table>
        </div> 

    - #### Vehicle Body Wooden Panels Produced Using a Laser Cutting Machine
        <div align=center>
        <table>
        <tr>
        <th>Lens Holder</th>
        <th>Vehicle Underfloor</th>
        <th>Vehicle Mid-Deck</th>
        <th>Vehicle Top Deck</th>
        </tr>
        <tr>
        <td></td>
        <td></td>
        <td></td>
        <td></td>
        </tr>
        </table>
        </div>

- ### The Production of Vehicle Support Frames Introduction - Using a 3D Printer
    - 3D printing is a manufacturing technology that builds objects layer by layer using a digital model.
    - We chose to use a 3D printer to manufacture the vehicle body because, compared to commercially available LEGO, 3D printing offers the advantage of not being bound by original specifications, providing increased freedom and flexibility in design. In contrast to products cut with a laser cutting machine, 3D printed components eliminate assembly issues and offer advantages in terms of lightweight construction.
    - Here is an introduction to the process of producing vehicle support frames using a 3D printer.

  - #### Stacked 3D Printer
   
    <div align=center>
    <table>
    <tr>
    <th>The Operational Status of the 3D Printer</th>
    <tr></tr>
    <td>3D-printer 3D_working </td>
    </tr>
    </table>
    
    <table>
    <tr align="center"><th colspan="4">The 3D Model and Physical Prototype of the Vehicle Chassis Designed for this Competition<th></tr>
    <tr align="center">
    <td>3D Photo File</td>
    <td>Top View</td>
    <td>Side View</td>
    <td>Vehicle Chassis Damage</td>
    <tr align="center">
    <td>file</td>
    <td>real</td>
    <td>real</td>
    <td>real</td>
    </tr>
    </table>
    </div>
        
     - The vehicle chassis produced using the 3D printer mentioned above was found to be prone to damage during collisions due to motor torque. As a result, we switched to using a Stereolithography (SLA) 3D printer to manufacture the required support frames for the vehicle, ensuring that the same issue does not occur during the competition."

  - #### Stereolithography (SLA) 3D Printer 

    - The working principle of a stereolithography (SLA) 3D printer is to project a UV light source onto a vat of liquid resin. The light cures the resin layer by layer until the entire object solidifies, known for its high precision and surface smoothness. They are typically used to manufacture highly precise and intricately structured objects.

    <div align="center">
    <table>
    <th> Stereolithography (SLA) 3D Printer</th><tr></tr>
    <td>Stereolithography_3D_Printer</td>
    </tr>
    </table>
    </div>

  - #### The process of using a Stereolithography (SLA) 3D Printer
    A stereolithography 3D printer may become unusable due to resin clogs if it is not regularly maintained, so it needs periodic cleaning. To understand how to maintain the machine, we sought advice from a senior student, who graciously gave us a hands-on demonstration.

    __Maintenance Process:__
    1. After the printing is complete, the finished product will be stuck to the build plate.
    2. Remove the build platform.
    3. Wipe off any resin adhering to the finished product.
    4. Clean the finished product with water.
    5. Spray alcohol to prevent an oily surface.
    6. Wipe off excess moisture and alcohol.
    7. Use a utility knife to remove the finished product from the platform.
    8. Remove any burrs from the finished product.
    9. Finally, clean the platform and restore the machine.

    <div align="center">
    <table>
    <tr>
    <td>Step 1</td>
    <td>Step 2</td> 
    <td>Step 3</td></tr>
    <tr align="center">
    <td></td>
    <td></td> 
    <td></td>
    </tr>
    <td>Step 4</td>
    <td>Step 5</td> 
    <td>Step 6</td></tr>
    <tr align="center">
    <td></td>
    <td></td>
    <td></td>
    </tr>
    <td>Step 7</td>
    <td>Step 8</td> 
    <td>Step 9</td></tr>
    <tr>
    <td></td>
    <td></td>
    <td></td>
    </tr>
    </table>
    </div>

   - Because the photocured parts are somewhat soft, we need to expose them to ultraviolet (UV) light for secondary curing, making the parts harder and less susceptible to deformation, which could affect the vehicle's movement.  

   <div align=center>
    <table>
    <tr>
    <th>Secondary Curing</th>
    </tr><tr>
    <td>light_again</td>
    </tr>
    </table>
    </div>

   - #### Comparison between Stacked 3D Printer and  Stereolithography (SLA) 3D Printer
     The following data was obtained during the experiment when printing the Ackermann steering mechanism. 
        <div align="center">
        <table>
        <tr align="center">
        <th rowspan="2">Photo</th>
        <th> Stacked 3D Printe</th>
        <th> Stereolithography (SLA) 3D Printer</th>
        </tr><tr align="center">
        <td></td>
        <td></td>
        </tr><tr align="">
        <td>The required printing time</td>
        <td>Faster</td>
        <td>Slower</td>
        </tr><tr>
        <td>Exterior</td>
        <td>Exterior with signs of layering</td>
        <td>Smooth</td>
        </tr><tr>
        <td>Hardness</td>
        <td>Dependent on the density</td>
        <td>Dependent on the exposure time</td>
        </tr>
        </table>
        </div>
 - ###  Onshpae Modle Draft- 3D Vehicle Modles
    - The vehicle chassis used in this competition was designed and developed by us using Onshape.
    <div align=center>
    <table>
    <tr>
    <th>3D Vehicle Chassis Design</th>
    <th>3d Vehicle Models</th>
    </tr><tr>
    <td></td> 
    <td></td> 
    </tr>
    </table>
    </div> 

    - ####  3D Vehicle Model Dimension Diagram
      <div align=center>
      <table>
      <tr>
      <th>Front Assembly</th>
      <th>Steering Knuckle</th>
      <th>Center Bearing Holder</th>
      <th>Out Bearing Holder</th>

    </tr><tr>
      <td>Front Assembly</td> 
      <td>Steering Knuckle</td> 
      <td>center_Bearing_Holder_size</td>
      <td>out_Bearing_Holder_size</td>
      </tr>
      </table>
      </div> 

  - ####  Vehicle body support components produced with Stereolithography (SLA) 3D Printer
      <div align=center>
      <table>
      <tr>
      <th>Front Assembly</th>
      <th>Steering Knuckle</th>
      <th>Bearing Holder</th>

      </tr><tr>
      <td>Front Assembly</td> 
      <td>Steering Knuckle</td> 
      <td>Bearing Holder</td>
      </tr>
      </table>
      </div> 

# <div align="center">HOME[Return Home](../../)</div>

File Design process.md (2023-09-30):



2023WRO Future Engineers Fire On All Cylinders  
====
# <div align="center">Design Porcess</div>

- In this technical document, a directory will be created based on vehicle production, and the directory titles will be hyperlinked so that viewers can access the content through links, making it easy to understand the core of the technical document and facilitate the rapid production of vehicles.

- ## Hardware selection
    - [Moter choise](https://github.com/kirkhu/WRO2023_FE-Shinan-Fire-On-All-Cylinders/blob/main/schemes/Motor/README.md)
    - [choose controller](https://github.com/kirkhu/WRO2023_FE-Shinan-Fire-On-All-Cylinders/tree/main/other/controller)
        - [Introduce Jetson Nano](https://github.com/kirkhu/WRO2023_FE-Shinan-Fire-On-All-Cylinders/tree/main/other/Jetson%20Nano)
        - [Introduce Raspberry pi](https://github.com/kirkhu/WRO2023_FE-Shinan-Fire-On-All-Cylinders/tree/main/other/Raspberry_Pi)
    - [Color sensor](https://github.com/kirkhu/WRO2023_FE-Shinan-Fire-On-All-Cylinders/blob/main/schemes/color_sensor/README.md)
    - [Introduction to Lidar](https://github.com/kirkhu/WRO2023_FE-Shinan-Fire-On-All-Cylinders/blob/main/schemes/Lidar/README.md)
    - [Camera](https://github.com/kirkhu/WRO2023_FE-Shinan-Fire-On-All-Cylinders/blob/main/schemes/Camera/README.md)
- ## Vehicle Design 
    - [BOM Parts List](https://github.com/kirkhu/WRO2023_FE-Shinan-Fire-On-All-Cylinders/tree/main/schemes/Parts_List#readme)
    - [Circuit Design](https://github.com/kirkhu/WRO2023_FE-Shinan-Fire-On-All-Cylinders/blob/main/models/Circuit_Design/README.md)
    - [Hardware Fool-Proof-Design](https://github.com/kirkhu/WRO2023_FE-Shinan-Fire-On-All-Cylinders/blob/main/schemes/fool-proof-design/README.md) 
    - [Fabricate the vehicle body](https://github.com/kirkhu/WRO2023_FE-Shinan-Fire-On-All-Cylinders/tree/main/models/Vehicle_2D-3D)
    - [Assembly Instructions & Diagrams](https://github.com/kirkhu/WRO2023_FE-Shinan-Fire-On-All-Cylinders/blob/main/schemes/Assembly_Instructions/README.md)  

    - __power Management__
      - [Power_supply_system](https://github.com/kirkhu/WRO2023_FE-Shinan-Fire-On-All-Cylinders/blob/main/schemes/Power_supply_system/README.md) 
      - [Li-Polymer Battery Safety Notice](https://github.com/kirkhu/WRO2023_FE-Shinan-Fire-On-All-Cylinders/blob/main/schemes/Li-Polymer_Battery/README.md)
- ## System Initialization 
    - [Software Platform Construction](https://github.com/kirkhu/WRO2023_FE-Shinan-Fire-On-All-Cylinders/blob/main/src/System_Platform%20_Software/README.md)
    - [Introduction to OpenCV](https://github.com/kirkhu/WRO2023_FE-Shinan-Fire-On-All-Cylinders/blob/main/other/OpenCV/README.md)
    - [Introduction to ROS](https://github.com/kirkhu/WRO2023_FE-Shinan-Fire-On-All-Cylinders/blob/main/other/ROS/README.md) 
- ## Obstacle Management 
    - __Image Processing and Predictions__
      - [Image Processing ](https://github.com/kirkhu/WRO2023_FE-Shinan-Fire-On-All-Cylinders/blob/main/src/Image_Processing_and_Predictions/README.md)  
      - [Steering overview ](https://github.com/kirkhu/WRO2023_FE-Shinan-Fire-On-All-Cylinders/blob/main/src/Steering_overview/README.md)  
    - __Programming__
      - [Open Challenge Code overview](https://github.com/kirkhu/WRO2023_FE-Shinan-Fire-On-All-Cylinders/tree/main/src/Programming/Open_Challenge)
      - [Obstacle Challenge Code overview](https://github.com/kirkhu/WRO2023_FE-Shinan-Fire-On-All-Cylinders/tree/main/src/Programming/Obstacle_Challenge)
      - [Distinctive Pseudo code](https://github.com/kirkhu/WRO2023_FE-Shinan-Fire-On-All-Cylinders/blob/main/src/Feature_Program/README.md)
- ## Photo 
    - [Team Photo](https://github.com/kirkhu/WRO2023_FE-Shinan-Fire-On-All-Cylinders/blob/main/t-photos/README.md) 
    - [Vehicle Photos](https://github.com/kirkhu/WRO2023_FE-Shinan-Fire-On-All-Cylinders/blob/main/v-photos/README.md) 
- ## Vehicle Operation Video 
    - [Open Challenge](https://github.com/kirkhu/WRO2023_FE-Shinan-Fire-On-All-Cylinders/blob/main/video/Open_Challenge/video.md)
    - [Obstacle Challenge](https://github.com/kirkhu/WRO2023_FE-Shinan-Fire-On-All-Cylinders/blob/main/video/Obstacle_Challenge/video.md)
- ## Work Dairy 
    - [March](https://github.com/kirkhu/WRO2023_FE-Shinan-Fire-On-All-Cylinders/tree/main/other/work_diary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)
    - [April](https://github.com/kirkhu/WRO2023_FE-Shinan-Fire-On-All-Cylinders/tree/main/other/work_diary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)
    - [May](https://github.com/kirkhu/WRO2023_FE-Shinan-Fire-On-All-Cylinders/tree/main/other/work_diary#20230501-20230507)
    - [June](https://github.com/kirkhu/WRO2023_FE-Shinan-Fire-On-All-Cylinders/tree/main/other/work_diary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)
    - [July](https://github.com/kirkhu/WRO2023_FE-Shinan-Fire-On-All-Cylinders/tree/main/other/work_diary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)
    - [August](https://github.com/kirkhu/WRO2023_FE-Shinan-Fire-On-All-Cylinders/tree/main/other/work_diary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)
    - [September](https://github.com/kirkhu/WRO2023_FE-Shinan-Fire-On-All-Cylinders/tree/main/other/work_diary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)

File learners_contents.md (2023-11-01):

<div align="center">logo</div> 

## For Learners ## 

- ### Hardware Selection
    - [Controller Selection](https://github.com/kirkhu/WRO2023_FE-Shinan-Fire-On-All-Cylinders/tree/main/other/Controller_Choosing)
    - [Moter Selection](https://github.com/kirkhu/WRO2023_FE-Shinan-Fire-On-All-Cylinders/blob/main/schemes/Motor/README.md)
    - [Color Sensor](https://github.com/kirkhu/WRO2023_FE-Shinan-Fire-On-All-Cylinders/blob/main/schemes/color_sensor/README.md)
    - [Lidar Selection](https://github.com/kirkhu/WRO2023_FE-Shinan-Fire-On-All-Cylinders/blob/main/schemes/Lidar/README.md)
    - [Camera Selection](https://github.com/kirkhu/WRO2023_FE-Shinan-Fire-On-All-Cylinders/blob/main/schemes/Camera/README.md)
    
- ### Vehicle Design
    - [Vehicle 2D/3D Models in CAD](https://github.com/kirkhu/WRO2023_FE-Shinan-Fire-On-All-Cylinders/tree/main/models/Vehicle_2D_3D)
    - [BOM Parts List](https://github.com/kirkhu/WRO2023_FE-Shinan-Fire-On-All-Cylinders/tree/main/schemes/Parts_List#readme)
    - [Vehicle Chassis Design Process](https://github.com/kirkhu/WRO2023_FE-Shinan-Fire-On-All-Cylinders/tree/main/schemes/Vehicle_Chassis_Design)
    - [Circuit Design](https://github.com/kirkhu/WRO2023_FE-Shinan-Fire-On-All-Cylinders/blob/main/models/Circuit_Design/README.md)
    - [Hardware Fool-Proof Design](https://github.com/kirkhu/WRO2023_FE-Shinan-Fire-On-All-Cylinders/blob/main/schemes/fool-proof-design/README.md) 
    - [Assembly Instructions & Wiring Diagrams](https://github.com/kirkhu/WRO2023_FE-Shinan-Fire-On-All-Cylinders/blob/main/schemes/Assembly_Instructions/README.md)
    - __power Management__
      - [Power Supply System](https://github.com/kirkhu/WRO2023_FE-Shinan-Fire-On-All-Cylinders/blob/main/schemes/Power_supply_system/README.md) 
      - [Li-Polymer Battery Low Voltage Alarm and Charging Equipment](https://github.com/kirkhu/WRO2023_FE-Shinan-Fire-On-All-Cylinders/blob/main/schemes/Li-Polymer_Battery/README.md)
- ### System Initialization
    - [OpenCV Introduction](https://github.com/kirkhu/WRO2023_FE-Shinan-Fire-On-All-Cylinders/blob/main/other/OpenCV/README.md)
    - [ROS Introduction](https://github.com/kirkhu/WRO2023_FE-Shinan-Fire-On-All-Cylinders/blob/main/other/ROS/README.md) 
    - [Software Platform Construction](https://github.com/kirkhu/WRO2023_FE-Shinan-Fire-On-All-Cylinders/tree/main/src/System_Platform_Software)
- ### Obstacle Management
    - __Image Processing and Predictions__
      - [Image Processing](https://github.com/kirkhu/WRO2023_FE-Shinan-Fire-On-All-Cylinders/tree/main/src/Image_Processing_and_Steering/Image_Processing)  
      - [Steering Overview ](https://github.com/kirkhu/WRO2023_FE-Shinan-Fire-On-All-Cylinders/tree/main/src/Image_Processing_and_Steering/Steering_overview)  
    - __Programming__
      - [Open Challenge Code Overview](https://github.com/kirkhu/WRO2023_FE-Shinan-Fire-On-All-Cylinders/tree/main/src/Programming/Open_Challenge)
      - [Obstacle Challenge Code Overview](https://github.com/kirkhu/WRO2023_FE-Shinan-Fire-On-All-Cylinders/tree/main/src/Programming/Obstacle_Challenge)
      - [Distinctive Pseudo Code](https://github.com/kirkhu/WRO2023_FE-Shinan-Fire-On-All-Cylinders/tree/main/src/Distinctive_Pseudo_Code)
- ### Pictures – Team and vehicle
    - [Team Members Introduction](https://github.com/kirkhu/WRO2023_FE-Shinan-Fire-On-All-Cylinders/blob/main/t-photos/README.md) 
    - [Vehicle Photos](https://github.com/kirkhu/WRO2023_FE-Shinan-Fire-On-All-Cylinders/blob/main/v-photos/README.md) 
- ### Performance videos
    - [Open Challenge](https://github.com/kirkhu/WRO2023_FE-Shinan-Fire-On-All-Cylinders/blob/main/video/Open_Challenge/video.md)
    - [Obstacle Challenge](https://github.com/kirkhu/WRO2023_FE-Shinan-Fire-On-All-Cylinders/blob/main/video/Obstacle_Challenge/video.md)
    - [Self-Driving Car Design Process Video](https://github.com/kirkhu/WRO2023_FE-Shinan-Fire-On-All-Cylinders/blob/main/video/ALL_video/video.md)
- ### GitHub Utilization
    - [GitHub Edit(VScode Edit/GIT)](https://github.com/kirkhu/WRO2023_FE-Shinan-Fire-On-All-Cylinders/blob/main/src/GitHub_Edit/README.md)
    - [GitHub Web Editing Languages](https://github.com/kirkhu/WRO2023_FE-Shinan-Fire-On-All-Cylinders/blob/main/src/GitHub_Languages/README.md)
- ### Work Dairy
    - [March](https://github.com/kirkhu/WRO2023_FE-Shinan-Fire-On-All-Cylinders/tree/main/other/work_diary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)
    - [April](https://github.com/kirkhu/WRO2023_FE-Shinan-Fire-On-All-Cylinders/tree/main/other/work_diary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)
    - [May](https://github.com/kirkhu/WRO2023_FE-Shinan-Fire-On-All-Cylinders/tree/main/other/work_diary#20230501-20230507)
    - [June](https://github.com/kirkhu/WRO2023_FE-Shinan-Fire-On-All-Cylinders/tree/main/other/work_diary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)
    - [July](https://github.com/kirkhu/WRO2023_FE-Shinan-Fire-On-All-Cylinders/tree/main/other/work_diary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)
    - [August](https://github.com/kirkhu/WRO2023_FE-Shinan-Fire-On-All-Cylinders/tree/main/other/work_diary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)
    - [September](https://github.com/kirkhu/WRO2023_FE-Shinan-Fire-On-All-Cylinders/tree/main/other/work_diary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)
    - [October](https://github.com/kirkhu/WRO2023_FE-Shinan-Fire-On-All-Cylinders/tree/main/other/work_diary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)
- ### ${{\color{red} Competition Schedule}} $  
# <div align="center">Gantt chart</div>

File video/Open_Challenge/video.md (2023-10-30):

<div align="center">logo</div>

## <div align="center">Testing Video of Self-Driving Car in Open Challenge</div> 

  Here are test videos of vehicles in different power and field combinations.

- ### Full width

  This is a test video of a vehicle in a field set to "wide-wide-wide-wide".

|Power 50 |Power 70|
|:----:|:----:|
|Open Challenge power 50 Full width On-All-Cylinders (https://youtu.be/OUg0x4Qdc0c "Open_Challenge_power_50_Full_width")|Open Challenge power 70 Full width On-All-Cylinders (https://youtu.be/MA1k2P87LdE "Open Challenge power 70 Full width On-All-Cylinders")|

- ### Half-width half-height
 
  This is a test video of a vehicle in a "wide-narrow-wide-narrow" field configuration, which is more difficult.
  
|Power 50 |Power 70|
|:----:|:----:|
|Open Challenge power 50 half-width half-height width On-All-Cylinders (https://youtu.be/7HdWxfWPfWc "Open Challenge power 50 half-width half-height width On-All-Cylinders")|Open Challenge power 70 half-width half-height width On-All-Cylinders (https://youtu.be/pcTpH8QgJFU "Open Challenge power 70 half-width half-height width On-All-Cylinders")|

- ### Full-width narrow
  This is a testing video of the vehicle on a course set as 'narrow-narrow-narrow-narrow.' As all road widths have been reduced, this results in a limited correction space for the machine, making it easy for it to overshoot during turns and potentially collide with the walls.

|Power 50 |Power 70|
|:----:|:----:|
|Open Challenge power 50 full-width narrow On-All-Cylinders (https://youtu.be/QaYUrrdAtE8 "Open Challenge power 50 full-width narrow On-All-Cylinders")|Open Challenge power 70 full-width narrow On-All-Cylinders (https://youtu.be/QtpuHt05MDg "Open Challenge power 70 full-width narrow On-All-Cylinders")|

- ### wide narrow wide narrow

  These are test videos of a vehicle in a "wide-narrow-wide-narrow" field configuration, recorded clockwise and counterclockwise.

|Clockwise|Counter Clockwise|
|:---:|:---:|
|Open Challange Countclockwise (https://youtu.be/rzolv8BAnoE "Open Challange Countclockwise") |Open Challange Countclockwise (https://youtu.be/HQ7YA0zPUbA "Open Challange Countclockwise")|
# <div align="center">HOME[Return Home](../../)</div>

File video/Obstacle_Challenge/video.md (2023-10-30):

<div align="center">logo</div>

## <div align="center">Testing Video of Self-Driving Car in Obstacle Challenge</div>

- #### The last traffic light on the second lap is a green signal.(No need to turn around ) 

  Here is a test video of a vehicle on the second lap, with the last traffic light being green. 

|The last traffic light on the second lap is a green signal.|
|:---:|
|Obstacle Challenge noRed@Shinan-Fire-On-All-Cylinders (https://youtu.be/DJtCfLO1X_A "Obstacle Challenge noRed@Shinan-Fire-On-All-Cylinders")|

- #### The last traffic light on the second lap is red.(Need to turn around)  

  Here are test videos of the last traffic light being red in different positions on the second lap.  

|At Position 1|At Position 2|At Position 3|
|:---:|:---:|:---:|
|Obstacle Challenge Red1@Shinan-Fire-On-All-Cylinders (https://youtu.be/1W0Gnmo7FZM "Obstacle Challenge Red1@Shinan-Fire-On-All-Cylinders")|Obstacle Challenge Red2@Shinan-Fire-On-All-Cylinders (https://youtu.be/fHehasALiVo "Obstacle Challenge Red2@Shinan-Fire-On-All-Cylinders")|Obstacle Challenge Red3@Shinan-Fire-On-All-Cylinders (https://youtu.be/uEku-8vA7zQ "Obstacle Challenge Red3@Shinan-Fire-On-All-Cylinders")|

 - ### Explanation to Obstacle Challenge

<div align="center">
  
Shina_Fire_On_Al_%20Cyliders (https://youtu.be/7WiBLkQUE0Q "Shina_Fire_On_Al_%20Cyliders")
</div>

# <div align="center">HOME[Return Home](../../)</div>

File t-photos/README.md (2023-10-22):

<div align="center">logo</div>

## <div align="center"> Team Members Introduction</div>
- ### Team Photo  

  Today is the first day of our team's establishment, so we took this photo as a commemoration. The location was chosen at the playground of the school where our club is located.

<div align="center">

|||
|:----:|:----:|

 </div>  

- ### Funny Photo  
  This photo was taken while we were attempting to lift our classmates LIN JHONG-BIN. In fact, it was a bit difficult to lift them, and we almost dropped him.

  

## Team Members of Introduction  
| | |
| :----: | :----: |
| __HU,YUN-RUEI__  | __Work Assignments：__ Report recording and writing.|
| Personal photo | Work photo |
|  |  |
| __LIN,JHONG-BIN__  | __Work Assignments：__ Code writing.|
|  Personal photo  |  Work photo  | 
|  |  |
| __ZHAO,ZHEN-BO__  |  __Work Assignments：__ Hardware design. |
| Personal photo |  Work photo  | 
|  |  |  

# <div align="center">HOME[Return Home](../)</div>

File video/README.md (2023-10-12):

<div align="center">logo</div>

# <div align="center">Demonstration Video  </div> 

## (video.md)  

> This directory must contain the video.md file with a URL to YouTube (should be either public or accessible by link) showing the vehicle driving autonomously. That part of the video where driving demonstration exists must be at least 30 seconds in length.

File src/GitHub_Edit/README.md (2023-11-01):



## <div align="center">GitHub's Editing Process </div>
__There are two ways to edit GitHub repositories:__ one is to edit directly on the GitHub website, which is called online editing, and the other is to use software like VS Code + Git on your local computer for offline editing, and then synchronize the changes to GitHub.

- #### Online Editing on GitHub Website:
  This is the simplest method. You can log in to your GitHub account using a web browser, navigate to the file you want to edit, and click the pencil icon on the top right corner to start editing. During online editing, you can directly modify the file content and submit the changes when you are done. GitHub will automatically create a new commit and apply the changes to the main branch or the branch you choose.
<div align="center">  
  
|||
|:---:|:---:|
</div>

- #### Offline Editing with VS Code + Git:
  This method requires you to install specific software, such as Visual Studio Code (VS Code) and Git, on your local computer. First, you need to download and install VS Code and Git. Next, you can open your GitHub repository in VS Code and make modifications to the desired file. After completing the edits, you need to use Git commands to push your local changes to the remote GitHub repository. This way, the file on GitHub will be updated to reflect the edits you made on your local machine.  

|Git| Git_bash|VS Code| VS Code Git|
|:---:|:---:|:---:|:---:|
|git|git_bash|vscode|git|

  In summary, both methods allow you to edit and synchronize files on GitHub. Online editing is suitable for simple changes, while offline editing provides more features and flexibility, making it particularly useful for handling larger projects and collaborative work. However, it's worth noting that online editing might be less intuitive when it comes to creating file folders compared to local editing. As a result, our team primarily uses local editing with online editing as a supplementary approach when editing GitHub repositories.  

- ### Introduction to Code Editor Software(Visal Studio Code) 

  - Visual Studio Code (often referred to as VS Code) is a free, open-source, and cross-platform code editor developed by Microsoft. It supports multiple programming languages and offers a rich set of extensions to cater to individual needs.
  - VS Code features an intuitive user interface and powerful code editing capabilities, including intelligent code completion, code navigation, debugging, and version control. It is widely embraced by developers and has become the preferred editing tool for many software development projects.

  __Therefore, we have chosen VS Code as the programming tool for the self-driving vehicle.__

  - Software Link：[Visal Studio Code](https://code.visualstudio.com/) 

# <div align="center">HOME[Return Home](../../)</div>

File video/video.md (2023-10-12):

<div align="center">logo</div>

## <div align="center">Demonstration Video(自走車各任務完成影片)</div> 
- ### Open Challenge(資格賽影片)
2023WRO Future-Engineers_qualifying-round (https://youtu.be/Z78iSG1QYfs "2023WRO Future-Engineers_qualifying-round") 

- ### Obstacle Challenge(任務賽影片)
2023WRO Future-Engineers_Obstacle Challenge (https://youtu.be/CwvGDfQJ8cQ "2023WRO Future-Engineers_Obstacle Challenge")

# <div align="center">HOME[Return Home](../)</div>  

> from kirk@snjh.tc.edu.tw

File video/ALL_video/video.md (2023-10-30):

<div align="center">logo</div>

## <div align="center">Self-Driving Car Design Process Video </div> 

The following video showcases the vehicle design and mission testing process.
   |Self-Driving Car Design Process Video|
   |:----:|
   |Self-Driving Car Design Process Video (https://youtu.be/VyvUaUY2K38 "Self-Driving Car Design Process Video")|

# <div align="center">HOME[Return Home](../../)</div>

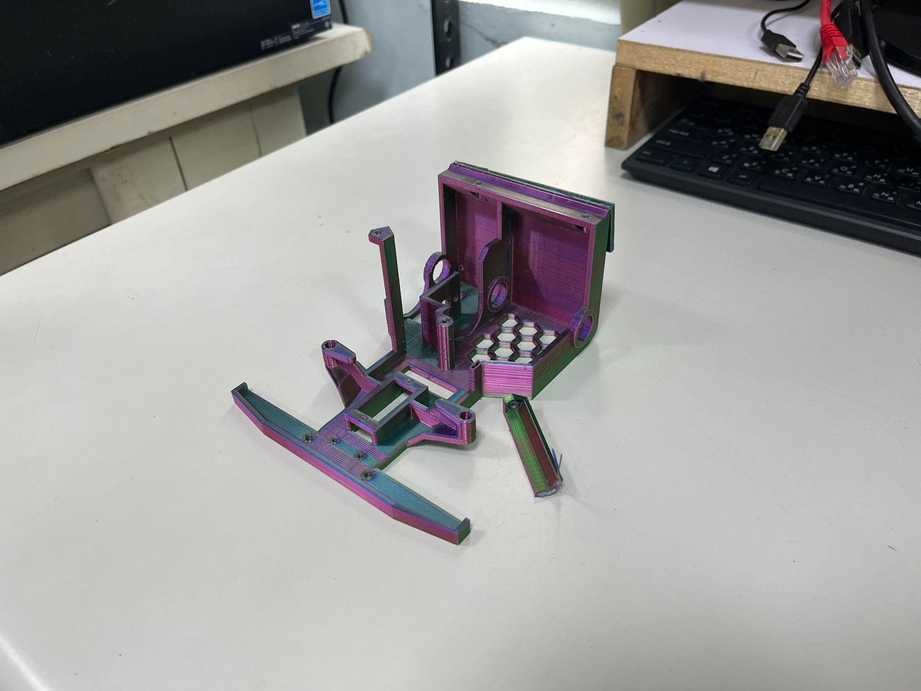
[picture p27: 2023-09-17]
schemes/Vehicle_Chassis_Design/img/3D-fracture.jpg

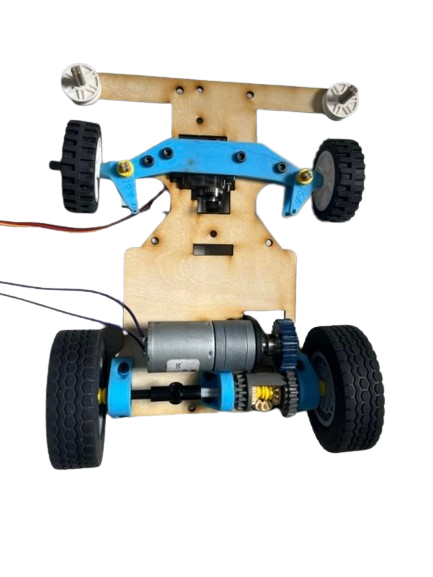
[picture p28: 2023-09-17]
schemes/Vehicle_Chassis_Design/img/3D_light_curing-removebg-preview.png

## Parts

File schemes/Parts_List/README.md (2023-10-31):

<div align="center">logo</div>  

# <div align="center">BOM Part List </div>
<li><a href="https://www.icshop.com.tw/product-page.php?27903" target="_blank"> Raspberry Pi 4B(8G)</a></li> 
<li><a href="https://atceiling.blogspot.com/2019/08/arduino54l293d.html" target="_blank">L293d motor controller</a></li>
<li><a href="https://abra-electronics.com/electromechanical/motors/gear-motors/metal-gearmotors/jga25-370-series/jga25-370-24v-620rpm-jga25-370-geared-dc-motor-for-diy-projects-a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">JGA25-370 620RPM DC reduction motor</a></li>  
<li>Black motor mounting bracket<br></li>  
<li>24-tooth Plastic gear<br></li>
<li><a href="https://www.amazon.com/-/zh_TW/dp/B0BFQLNDPM">MG90s servo motor</a></li>    
<li><a href="https://www.amazon.ae/XLX-B3f-4055-Momentary-Tactile-Button/dp/B07NWDHH41">Button B3F-4055</a></li>  
<li><a href="https://www.amazon.in/Invento-Battery-Voltage-Indicator-Checker/dp/B072V44Q5Z">Lipo battery low voltage alarm </a></li>  
<li><a href="https://shopee.tw/%E6%90%96%E9%A0%AD%E9%96%8B%E9%97%9C-3A-250VAC-6A-125VAC-MTS-1%E9%80%A3%E5%8B%95%E9%96%8B%E9%97%9C-B5031-%E5%A4%A7%E6%B4%8B%E5%9C%8B%E9%9A%9B%E9%9B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" target="_blank">switch AC 725W</a></li>     
<li><a href="https://shopee.tw/TW1678-IMX219-D160-800%E8%90%AC%E5%83%8F%E7%B4%A0%E6%94%9D%E5%83%8F%E9%A0%AD-%E8%A6%96%E8%A7%92160%E5%BA%A6-Jetson-Nano%E3%80%81Pi-Camera-i.6760059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" target="_blank">SONY IMX219</a></li>
<li><a href="https://tw.bid.yahoo.com/item/100634748049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" target="_blank">Wide-angle camera module </a></li>
<li><a href="https://shopee.tw/product/17393576/2036942264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">Li-Polymer battery 3S Desire Power V8 11.1V 1300mAh 70C </a></li>
<li>Amass TX60-M plug<br></li>
<li><a href="https://www.amazon.com/NOYITO-DC-DC-Power-Supply-Module/dp/B07G456MS8">High Current 5A Constant Voltage Constant Current Buck Power Supply Module</a></li>  
<li><a href="https://www.amazon.com/-/zh_TW/TCS34725/dp/B0BBLXXJ4Q">TCS34725 RGB color sensor</a></li>
<li><a href="https://www.robotshop.com/products/ldrobot-d100-lidar-kit">Lidar D100</a></li>
<li>USB to TTL CP2102<br></li>  
<li>Ribbon cable 15 pin 30 cm spacing 0.1<br></li>
<li>Lego 6573 Differential Gear<br></li>
<li>695ZZ M5x13x4 bearing NSK<br></li>
<li>Iron wire 1.2mm 1.2mm<br></li>
<li>Flat cable female-to-female 40p(20x2)<br></li>
<li>Press-fit right-angle male socket 40p(20x2)<br></li>
<li>white socket 2p<br></li>
<li>white socket 3p<br></li>
<li>white socket 4p<br></li>
<li>white socket 6p<br></li>
<li>Female socket 2.45mm<br></li>
<li>Male socket 2.45mm<br></li>
<li>plastic column M3x6mm column length 30mm<br></li>
<li>plastic column M3x6mm column length 20mm<br></li>
<li>plastic column M3x6mm column length 12mm<br></li>
<li>plastic column M3x6mm column length 6mm<br></li>
<li>Internal Phillips Head Plastic screw M3x5mm<br></li>
<li>Internal Phillips Head Plastic screw M3x20mm<br></li>
<li>Plastic Nut M3<br></li>
<li>Internal Hexagonal Metal Screw M3x10mm<br></li>
<li>Internal Hexagonal Metal Screw M3x12mm<br></li>
<li>matal Nut M3<br></li>
<li>Internal Phillips Head Metal Screw M2x14mm<br></li>
<li>Internal Phillips Head Metal Screw M2x12mm<br></li>
<li>Internal Phillips Head Metal Screw M2x4mm<br></li>
<li>Matal Nut M2<br></li>
<li>Cross recessed round head Metal screw M2x10mm<br></li>
<li>pegboard 30x48 hole 90x150 mm<br></li>
<li>Light Curing Resin UV-604<br></li>
<li>wood broad Thickness of 3mm<br></li>

# <div align="center">HOME[Return Home](../../)</div>

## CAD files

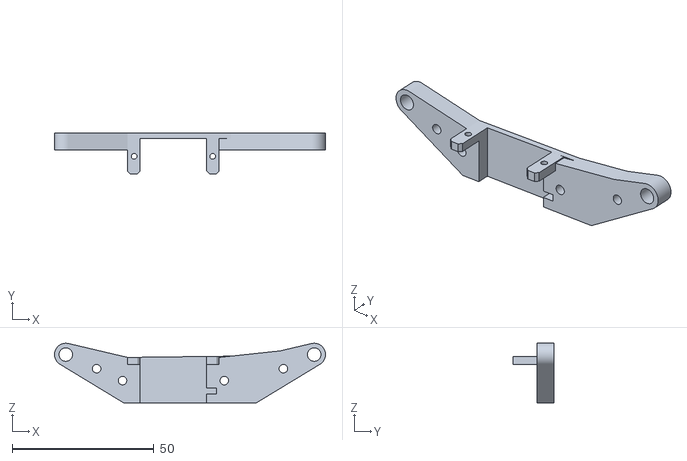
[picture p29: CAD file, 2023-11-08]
models/Vehicle_2D_3D/Steering Holdor.STL
95.6 x 14.5 x 21.0

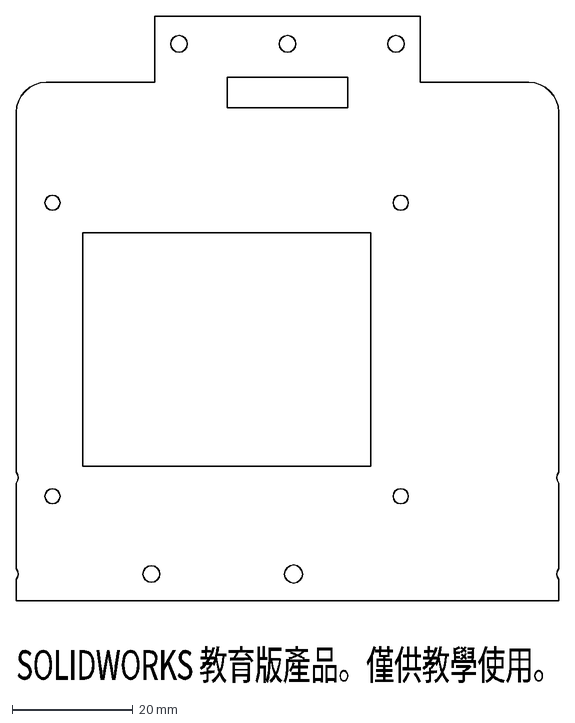
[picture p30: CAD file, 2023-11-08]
models/Vehicle_2D_3D/Vehicle_Chassis_Sizse/Body-middle-RPi.DXF
SOLIDWORKS 教育版產品。僅供教學使用。

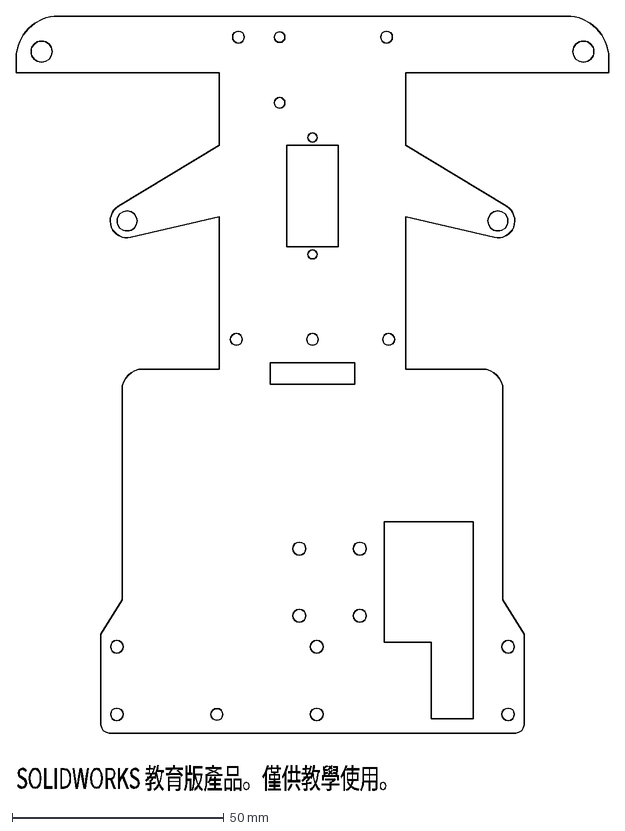
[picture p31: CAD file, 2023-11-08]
models/Vehicle_2D_3D/Vehicle_Chassis_Sizse/Body-Bottom-RPi.DXF
SOLIDWORKS 教育版產品。僅供教學使用。

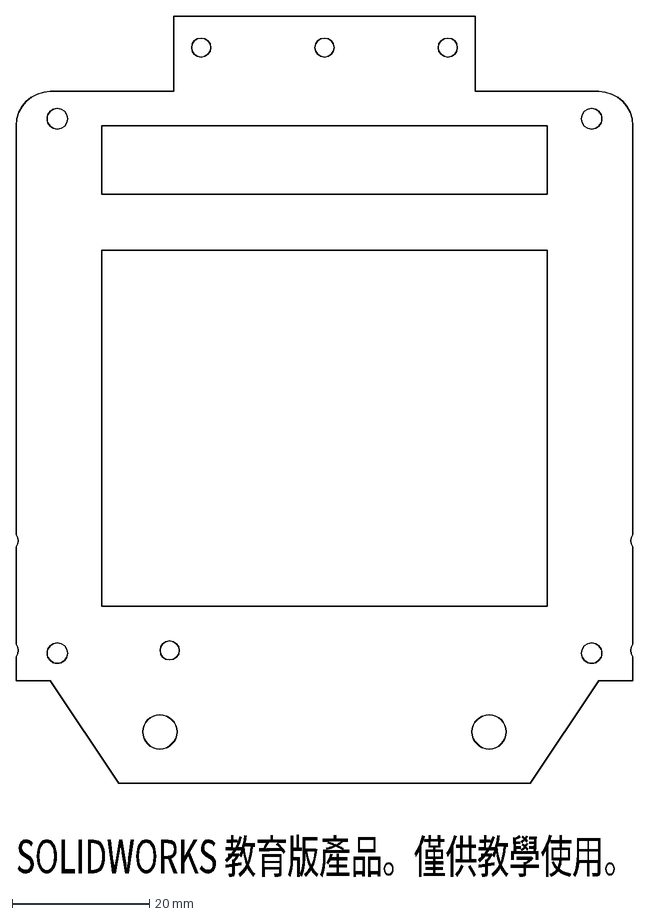
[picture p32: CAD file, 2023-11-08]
models/Vehicle_2D_3D/Vehicle_Chassis_Sizse/Body-Top-RPi.DXF
SOLIDWORKS 教育版產品。僅供教學使用。

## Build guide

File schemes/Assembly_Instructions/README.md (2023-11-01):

<div align="center">logo</div>

## <div align="center">Hardware Assembly Instructions & Wiring Diagrams</div>
- ### Hardware Configuration of Electronic Equipment

  - The combination of electronic equipment configuration with the vehicle chassis structure forms a self-driving car.
  - The diagram below illustrates the placement of electronic equipment on the vehicle.
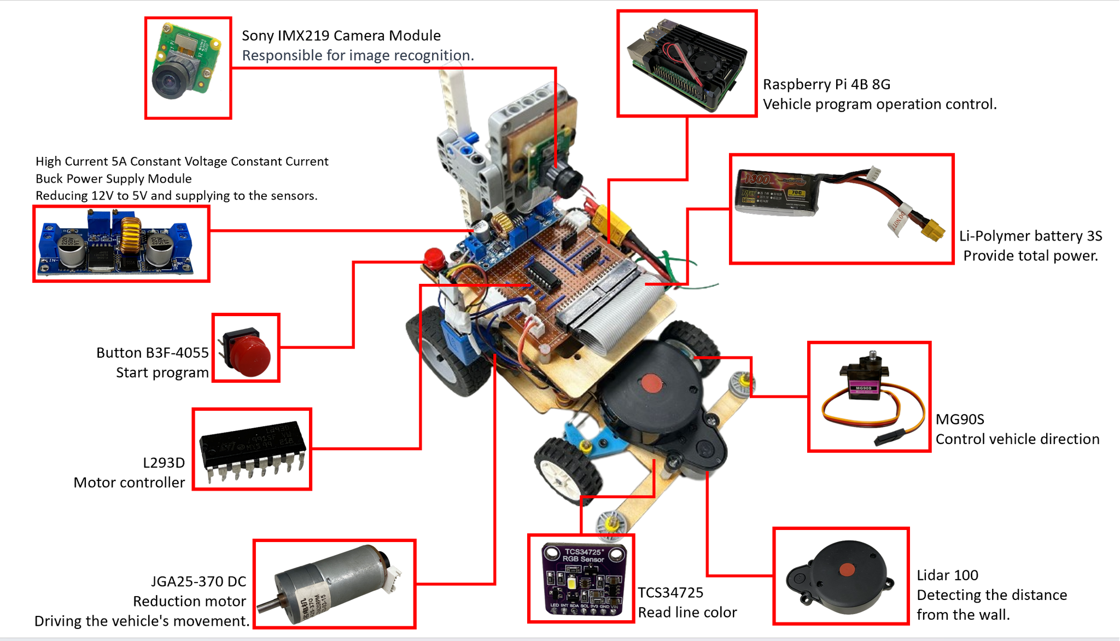
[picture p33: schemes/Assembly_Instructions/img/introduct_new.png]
Components's Position
  

- ### System Operation Process
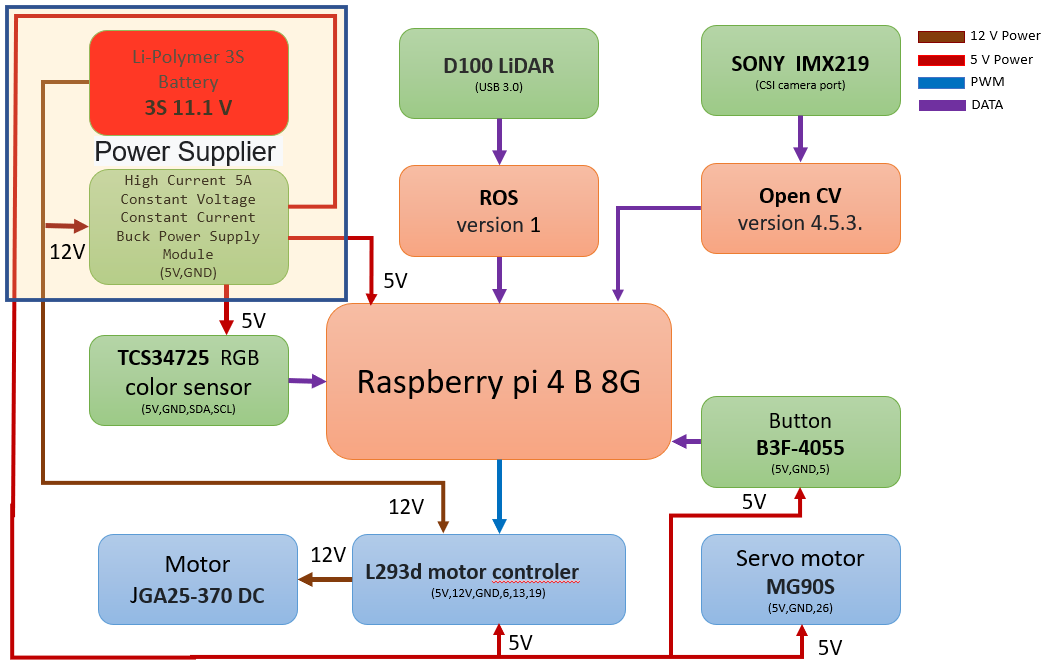
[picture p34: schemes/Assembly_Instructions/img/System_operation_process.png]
    

- The battery provides 12V power to the motor controller (L293D) and the voltage regulator. The voltage regulator steps down the voltage from 12V to 5V before supplying power to the Raspberry Pi and various sensors as their power source.  
- The LiDAR sensor detects distance values between the vehicle and walls in a 360-degree range. These values are transmitted to the Raspberry Pi via ROS for computation. The control signals are then sent to the front wheel servo motor (MG90S) to control the direction of movement.  
- The Sony IMX219 camera transmits images to the Raspberry Pi, which then uses OpenCV for image recognition. The control signals are then sent to the front wheel servo motor (MG90S) to control the direction of movement for obstacle avoidance.  
- The color sensor is used to identify the blue, orange, and white areas on the track. It reads the color values and transmits them to the Raspberry Pi for computation. This information is used to count the laps of the vehicle on the track.
- ### Vehicle Body Structure Display Diagram
  <div align="center">
  <table>
    <tr>
        <th>Top View of the Overall Apparatus</th>
        <th>Middle Layer Structure Top View</th>
        <th>Top View of Vehicle Chassis</th>
        <th>Bottom View of Vehicle Chassis</th>
    </tr>
    <tr align="center">
      <td>   </td><td></td><td></td>
      <td></td>
    </tr>
  </table>
  </div>

- ### Circuit Board 
<div align="center">
<table>
  <tr align="center">
      <th> Circuit Board of Top View </th><th>Circuit Board of Button View</th>
  </tr>
  <tr align="center">
     <td>  </td><td></td>
  </tr>
</table>
</div>

- ### Overview of Important Parts List
  - #### Raspberry Pi 4B 8G
    <table border=0 width=100% >
      <tr>
      <td >

    __Specification:__ 
    - Processor: Broadcom BCM2711, Quad-core Cortex-A72, 64-bit SoC, 1.5GHz
    -  Memory: 8GB LPDDR4 SDRAM
    -   Connectivity: Dual-band IEEE 802.11ac wireless + Bluetooth 5.0, Gigabit Ethernet, 2×USB 3.0, 2×USB 2.0 ports
    -   GPIO: Forward-compatible with Raspberry Pi's standard 40-pin GPIO
    -   Dimensions: 85.6×56.5×17.8mm
    -   Weight: 45 grams

    __Uses in Competition:__ 
    - Responsible for receiving data from color sensors, LiDAR, and images, processing recognition, and controlling the vehicle's direction and movement.
    </td>
       <td >
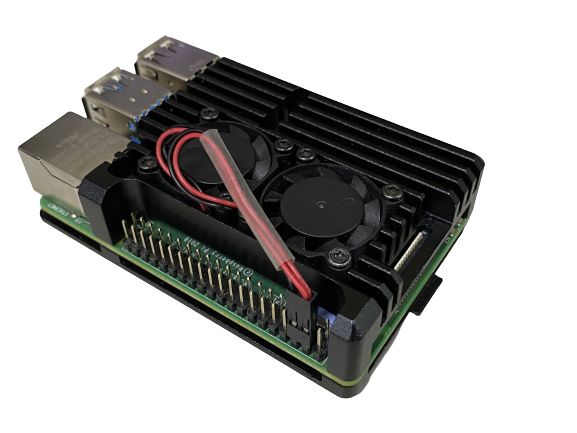
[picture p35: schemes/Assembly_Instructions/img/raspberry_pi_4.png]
Raspberry Pi 4B 8G
       
       </td>
      </tr>
    </table>

  - #### JGA25-370 DC Reduction Moto
    <table border=0 width=100% >
      <tr>
      <td > 

    __Specifications:__  
    - No-load Speed: 640 rpm  
    - Reduction Ratio: 1:34  
    - Operating Voltage: 6 - 12V  

    __Uses in Competition：__
    - Responsible for rotating the vehicle's rear wheels to enable it to move forward and backward.
    </td>
       <td >
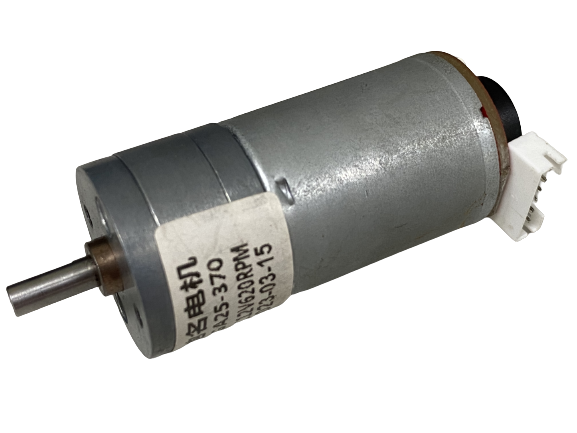
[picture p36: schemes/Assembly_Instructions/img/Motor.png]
GA25-370 DC reduction motor
       
        </td>
      </tr>
    </table>     
  - ### MG90S Servo Motor
    <table border=0 width=100% >
      <tr>
      <td>  

    __Specifications:__ 
    - Controllable Rotation Angle: 0-180°  
    - Maximum Torque: 2.0 kg/cm (at 4.8V)  
    - Fastest Rotation Speed: 0.11 seconds (at 4.8V)  
    - Operating Voltage: 4.8V - 7.2V  

    __Uses in Competition：__
    - Control the front wheel steering of the vehicle to enable it to turn while in motion. 
    </td>
        <td>
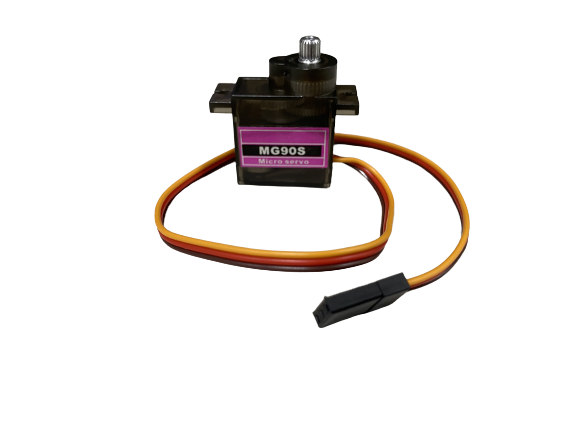
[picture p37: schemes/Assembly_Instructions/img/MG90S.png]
MG90S servo motor伺服馬達
      
        </td>
      </tr>
    </table>

  - #### Dual H-bridge DC motor driver IC - L293D

    <table border=0 width=100% >
      <tr>
      <td>  

    __Specifications:__ 
    - 293D is a dual H-bridge DC motor driver IC that can be used to control two DC motors.
    - Wide operating voltage range: 4.5V to 36V.
    - Output current: 600 mA (continuous) and 1.2 A (peak) per channel.
    - Output voltage range: 3 V to 36 V.
      
    __Uses in Competition：__  
    - Drive the vehicle forward and backward by controlling the JGA25-370 DC gear motor
    </td>
       <td>
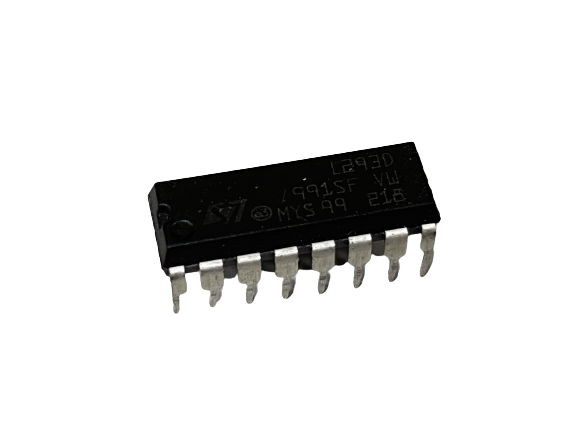
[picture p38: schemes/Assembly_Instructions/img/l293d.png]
L293d motor controler
      
       </td>
      </tr>
    </table>
  - #### Li-Polymer 3S Battery 
    <table border=0 width=100% >
      <tr>
        <td> 

    __Specifications:__
    - Maximum Current: 45.5A  
    - Net Weight: Approximately 107g  
    - Rated Voltage: 11.1V  

    __Uses in Competition：__  
    - Supply power to the vehicle for use.  
    </td>
        <td>
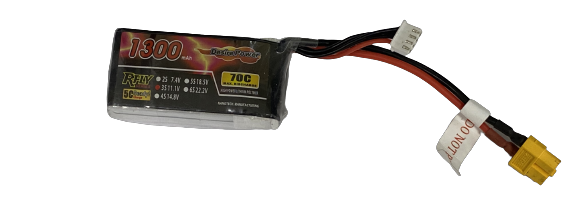
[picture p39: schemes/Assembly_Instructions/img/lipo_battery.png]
Li-Polymer 3S Batter
      
        </td>
      </tr>
    </table>

  - #### Button

    <table border=0 width=100% >
      <tr>
        <td>

    __Specifications:__ 
    - Operating Voltage: 3.3V - 5.0V  
    - Number of Pins: 3  
    - Output Signal: Digital  

    __Uses in Competition：__
    - Control the vehicle's start and drive switch.
    </td>
        <td>
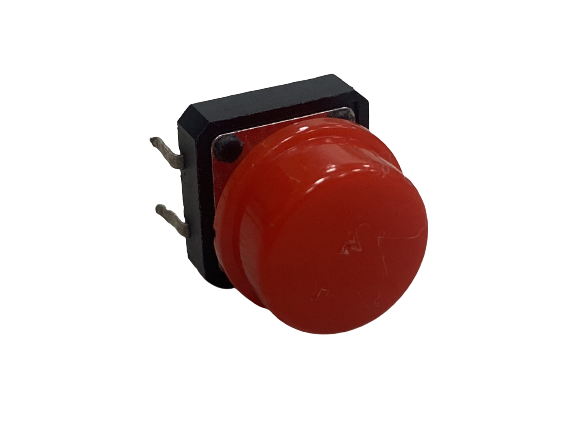
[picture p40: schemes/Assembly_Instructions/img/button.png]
Button( B3F-4055 微動輕觸開關)
       
        </td>
      </tr>
    </table>

  - #### High Current 5A Constant Voltage Constant Current Buck Power Supply Module 

    <table border=0 width=100% >
      <tr>
        <td> 

    __Specifications:__ 
    - Input Voltage: 4.0V - 38.0V  
    - Output Voltage: 1.25V - 36.0V  
    - Operating Frequency: 180Hz  

    __Uses in Competition：__  
    - Step down the battery voltage from 11.1V to 5V to provide the required voltage for the vehicle's electronic devices.
    </td>
        <td>
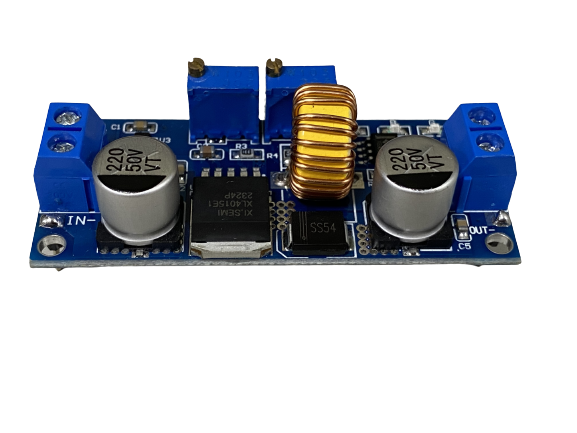
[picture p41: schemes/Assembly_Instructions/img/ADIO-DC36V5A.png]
High Current 5A Constant Voltage Constant Current Buck Power Supply Module(大電流5A恆壓恆流降壓電源模組)
       
        </td>
      </tr>
    </table>

  - #### TCS34725 RGB Color Sensor
    <table border=0 width=100% >
      <tr>
        <td > 

    __Specifications:__  

    - Operating Voltage: 3.3V - 5.0V 
    - Output resolution: 16 bits
    - Dynamic range: 3.8M:1
    - Sensitivity: 100 μV/lux
    - Interface: I2C interface  

    __Uses in Competition：__  
    - Responsible for detecting the blue and orange lines as well as the white areas on the field.

    </td>
        <td>
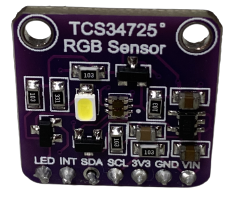
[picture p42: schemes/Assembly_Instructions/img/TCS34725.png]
TCS34725 RGB color sensor
       
        </td>
      </tr>
    </table>

  - #### SNOY IMX 219 Camera Module
    <table border=0 width="100%" >
      <tr>
        <td> 

    __Specifications:__ 
    - Viewing Angle: 160 degrees  
    - Effective pixels: 3280 x 2464
    - Total pixels: 3296 x 2512
    - Maximum aperture: F2.0
    - Focal length: 2.96mm
    - Interface: CSI (Camera Serial Interface)  

    __Uses in Competition：__  
    - Collecting images for image recognition. Responsible for collecting images and transmitting them to the Raspberry Pi for image recognition.
    </td>
       <td >
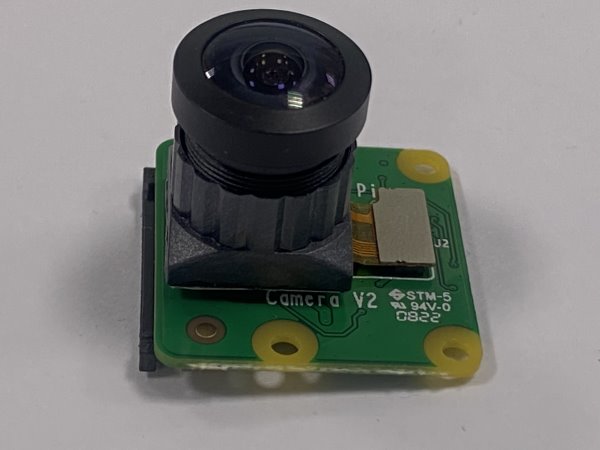
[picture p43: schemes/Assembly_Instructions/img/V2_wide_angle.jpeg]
SNOY IMX 219 Lens module
        
        </td>
      </tr>
    </table>

  - ### D100 LiDAR
    <table border=0 width=100% >
      <tr>
       <td> 

    __Specifications:__  
    - The D100 Developer Kit is built around the LiDAR LD14 as its core, complemented by related accessories.
    - It employs triangulation technology for a simple 360-degree full scan.
    - Angular Resolution: 1 degree.
    - Maximum measurement distance is 8 meters.
    - Detection frequency: 2300 Hz.
    - Dimensions: 96.3 x 59.8 x 38.8 mm.

    __Uses in Competition：__  
    - Used to detect obstacles in front and on the left and right sides, as well as to keep the vehicle centered in its lane. 
      </td>
      </td>
        <td>
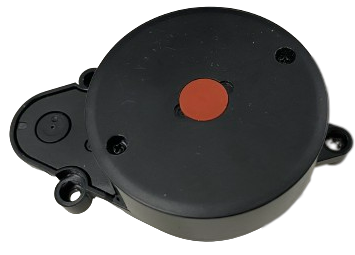
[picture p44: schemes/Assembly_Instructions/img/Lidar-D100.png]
D100 LiDAR(D100 光達)
          
        </td>
      </tr>
    </table>

# <div align="center">HOME[Return Home](../../)</div>

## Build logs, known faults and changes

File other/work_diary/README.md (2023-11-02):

<div align="center">logo</div>

# <div align="center">Work Diary </div> 
  Here is the record of the process for own design and manufacturing of vehicle and components, with off the shelf electrical components, such as motors and sensors.  
## 2023/03/19 ~ 2023/03/26  
**Member:**  ZHAO,ZHEN-BO、LIN,JHONG-BIN、HU,YUN-RUEI  
**Content:**  

At the outset, due to our uncertainty about how to initiate the process of constructing and assembling the vehicle, we turned to the official Donkey Car website for guidance. Consequently, the construction of the vehicle will be based on modifications to the vehicle design provided on the official website.

<div align="center">
<table>
<tr align="center">
<th><a href="https://www.donkeycar.com/">Donkey Car official website</a></th>
<th><a href="http://docs.donkeycar.com/">Donkey Car technical documentation</a></th>
</tr>
<tr align="center">
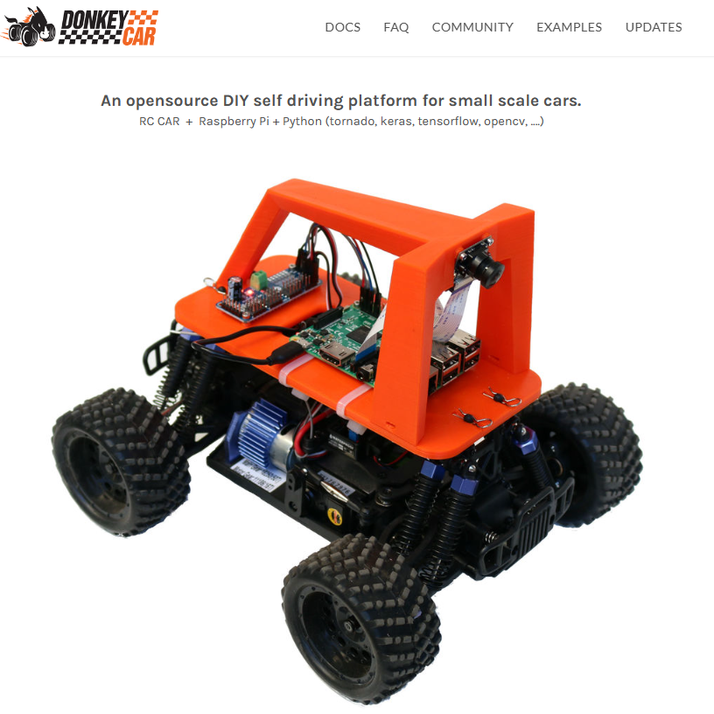
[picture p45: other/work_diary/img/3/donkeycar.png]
<td></td>
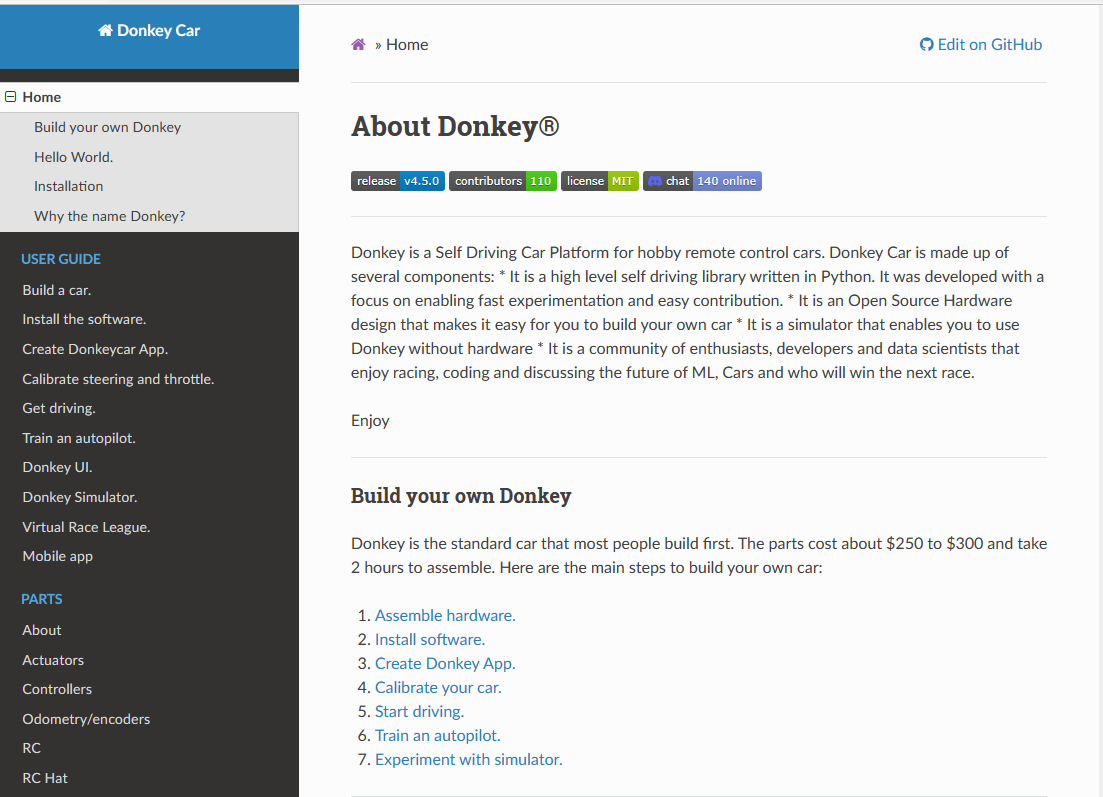
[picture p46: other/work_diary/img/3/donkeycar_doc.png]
<td></td>
</tr>
</table>
</div>
<div align="center" width=100%>
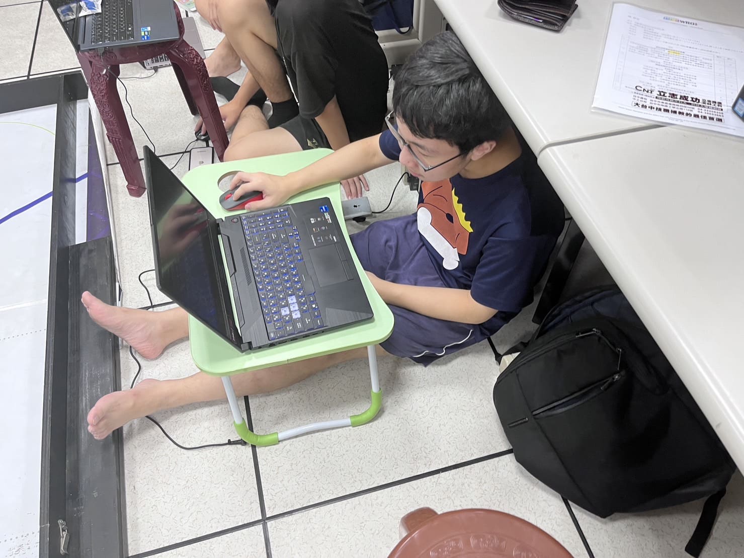
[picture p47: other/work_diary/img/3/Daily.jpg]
Daily

</div>

## 2023/03/27 ~ 2023/04/02
**Member:**  ZHAO,ZHEN-BO、LIN,JHONG-BIN、HU,YUN-RUEI  
**Content:**  
- To ensure the smooth progression of the competition, our team carefully planned the completion timeline for each stage of the competition activities.
- After reading the rules, we began the process of selecting our controller. Upon reviewing previous competitions, we observed that the majority of participants used either Raspberry Pi or Jetson Nano as their controllers. Based on this information, I had to decide between these two options. Ultimately, I opted for the Raspberry Pi 4B due to its smaller size and more affordable price compared to the Jetson Nano.

  __Competition Activity Stages Work Completion Timeline Schedule(Gantt Chart)__ 
<div align="center" >
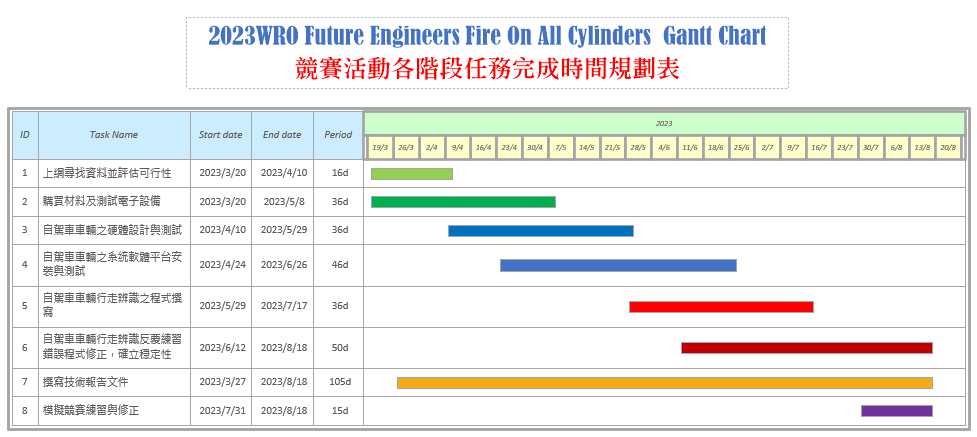
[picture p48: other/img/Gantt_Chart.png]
甘特圖
  
</div>

### Vehicle Computing Controller
<div align="center" >
<table >
<tr align="center">
<th>Raspberry pi 4 B 8G</th>
<th>Jeston Nano </th>
<tr align="center">
<td>
樹梅派</td>
<td>
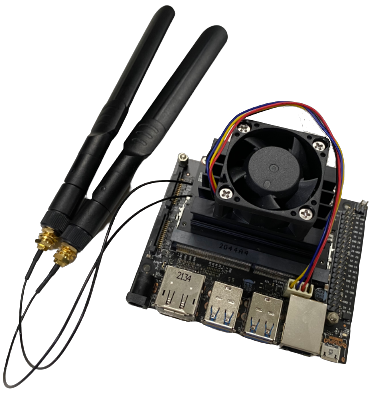
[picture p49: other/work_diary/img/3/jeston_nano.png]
jeston nano
</td>
</tr>
</table>
</div>

## 2023/04/03 ~ 2023/04/09  
**Member:**  ZHAO,ZHEN-BO、LIN,JHONG-BIN、HU,YUN-RUEI  
**Content:**  

- As we waited for the Raspberry Pi to initialize and the required libraries to be installed, we proceeded to choose the motor for propulsion. We had two options: the JGA25-370 and the JGA16-050. The JGA25-370 offers higher torque, making it suitable for moving heavier objects. On the other hand, the JGA16-050 is smaller and lighter but comes with relatively lower torque. Taking into account the anticipated weight of the robot, we decided to go with the higher torque of the JGA25-370 motor.
- Among the JGA25-370 options, there are several variations currently available within the club.
- While testing the motor's operation, we found that a simple application of positive and negative voltage did not offer effective control over the performance or speed adjustment of the JGA25-370 motor. Consequently, a motor controller was necessary to regulate the speed of the DC geared motor. We considered two options: the L293D chip and the L298N module. In order to keep the weight minimal, we opted for the compact L293D chip. Its small size enables us to integrate more sensors, ultimately saving space, reducing weight, and improving the robot's maneuverability.

#### DC Motor
<div align="center"><table><tr align="center">
<th rowspan="2">Model(model number)</th>
<th>JGA25 370</th>
<th>JGA25 370</th>
<th>JGA25 371</th>
<th>JGA16-050</th>
</tr>
<tr  align="center">

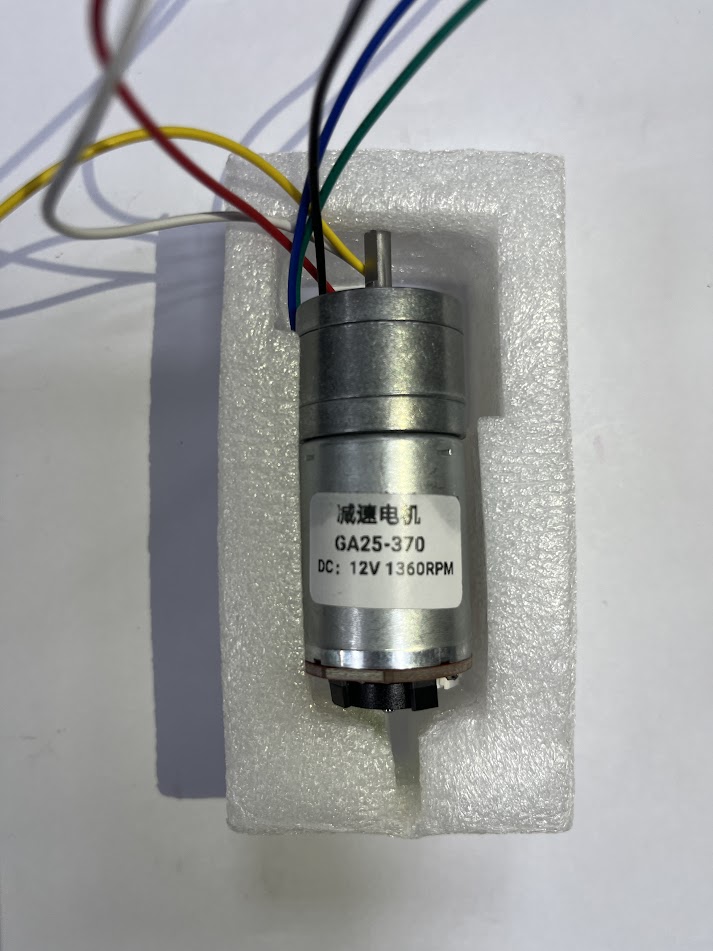
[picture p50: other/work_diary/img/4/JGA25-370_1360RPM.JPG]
JGA25-370_1360RPM
<td></td>
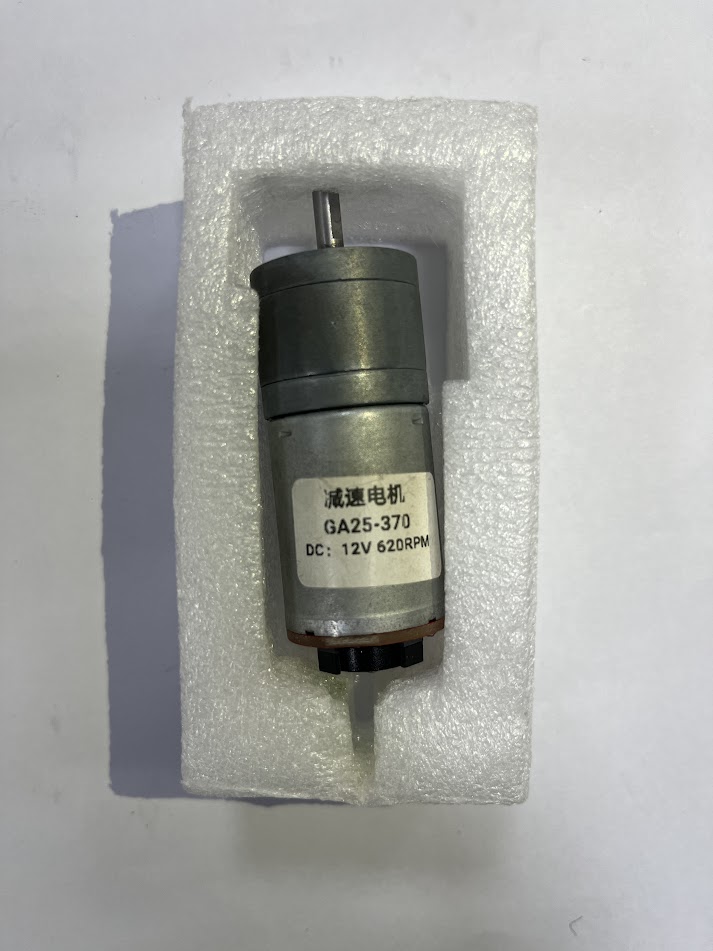
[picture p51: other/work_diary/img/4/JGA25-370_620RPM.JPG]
JGA25-370_620RPM
<td></td>
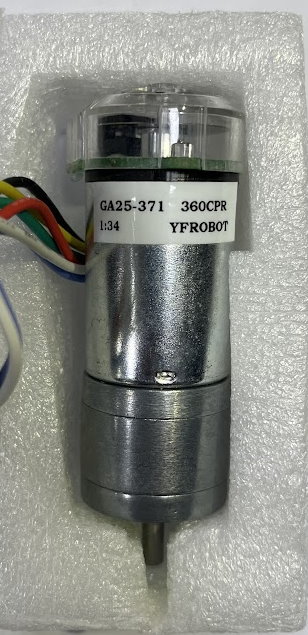
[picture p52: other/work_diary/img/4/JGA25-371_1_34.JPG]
JGA25-371M
<td></td>
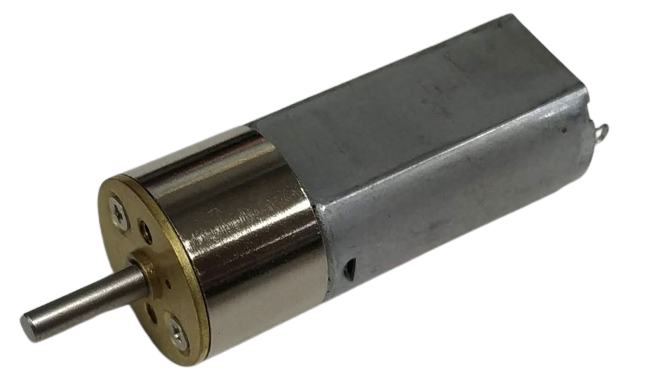
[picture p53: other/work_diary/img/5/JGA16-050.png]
JGA16-050
<td ></td>
</tr>
<tr align="center">
<td >speed</td>
<td >1360rpm/m</td>
<td >620rpm/m</td>
<td >294rpm/m</td>
<td >220rpm/m</td>
</tr>
<tr align="center">
<td>torque</td>
<td>4.27kg.cm</td>
<td>9.15kg.cm</td>
<td>5.2kg.cm</td><td>1.15kgcm</td>
</tr><tr align="center">
<td>power</td><td>5.4W</td><td>5.4W</td><td>4.2W</td><td>0.33W</td>
</tr>
</table>
</div>

## 2023/04/10 ~ 2023/04/16  
**Member:**  ZHAO,ZHEN-BO、LIN,JHONG-BIN、HU,YUN-RUEI  
**Content:**  

- Given the vehicle's continuous movement, a switch to battery power is necessary. Considering the motors' requirement of a 12V voltage for operation, selecting a battery with 12V voltage and 3V current is essential. Two alternatives are available: lithium-ion batteries (18650) and lithium polymer batteries (3S). However, the 18650 battery is bulkier and heavier, leading us to choose the lithium polymer battery for its space-saving and lightweight advantages.
- However, the maximum voltage supported by the Raspberry Pi is only 5.2V. Therefore, we need to use a voltage regulator module to reduce the voltage and prevent any potential damage to the Raspberry Pi. In our initial considerations, the LM2596 DC-DC adjustable voltage regulator module seemed promising due to its numerical display feature that indicates the current output voltage. Nonetheless, it's worth noting that this module has a maximum current capacity of only 3A. Considering our requirements, we decided to opt for a constant voltage and constant current step-down power supply module, capable of handling up to 5A. While this alternative lacks a numerical display, we have plans to integrate a low voltage alarm system to monitor the battery voltage closely and ensure its safety.
####  Batteries
<div align="center" width=100%>
<table >
<tr>
  <th> 18650 lithium batteries </th> <th>Li-Polymer 3S Battery 
  </th>
</tr>
<tr>
  <td>
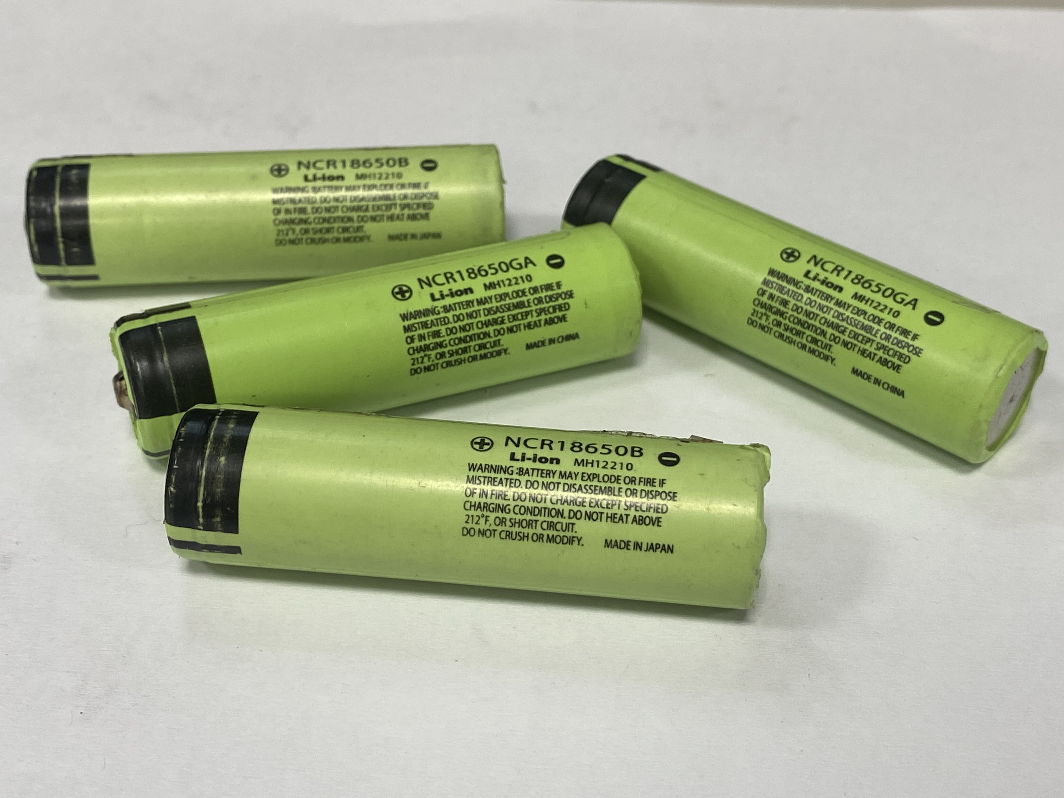
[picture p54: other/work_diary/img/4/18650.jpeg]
   </td>
  <td>
  lipo_battery
  </td>
</tr>
</table>
</div>

#### Voltage Regulator Module
<div align="center" width=100%>
<table >
<tr align="center">
  <th> LM2596 DC-DC Adjustable Buck Converter Module </th> 
  <th>5A Constant Voltage and Constant Current Buck Converter Module </th>
</tr>
<tr align="center">
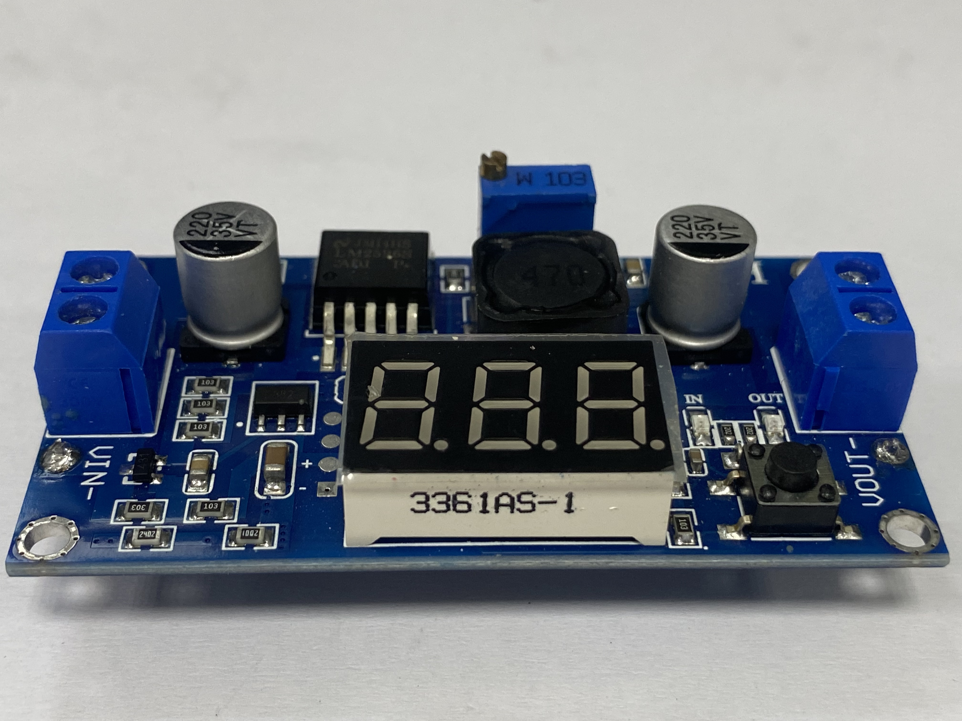
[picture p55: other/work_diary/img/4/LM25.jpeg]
  <td>    </td>
  <td>MG90S 
  </td>
  </tr>
</table>
</div>

#### Low Voltage Alarm
<div align="center" width=100%>
<table >
<tr align="center">
  <th> Low Voltage Alarm</th> 
</tr>
<tr align="center">
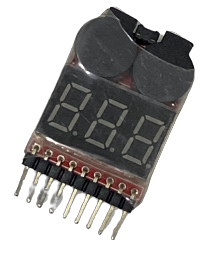
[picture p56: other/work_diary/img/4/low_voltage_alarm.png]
low_voltage_alarm
  <td></td>

  </tr>
</table>
</div>

## 2023/04/17 ~ 2023/04/23
**Member:**  ZHAO,ZHEN-BO、LIN,JHONG-BIN、HU,YUN-RUEI  
**Content:**    

- The next step is to choose the controlling motor. After searching for information online, we discovered that MG90S and SG90 are the most common options. The difference between MG90S and SG90 lies in the front gear, with the former being made of metal and the latter being made of plastic. Due to our frequent need for continuous rotation, we have selected the MG90S, as it is less prone to damage.

#### Servo Motor
<div align="center">
<table>
<tr align="center">
<th rowspan="2">Model(model number)</th>
<th> MG90S</th>
<th >SG90</th>
</tr>
<tr align="center">
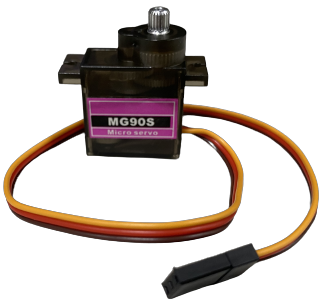
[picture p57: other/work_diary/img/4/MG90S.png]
<td></td>
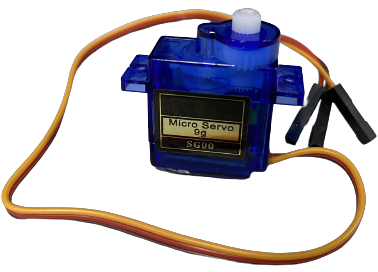
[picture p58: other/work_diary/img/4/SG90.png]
SG90
<td></td>
</tr>
<tr align="center">
<td>Rotation angle</td>
<td>90° MAX</td>
<td>0~90°/180° MAX</td>
</tr>
<tr align="center">
<td>Torque</td>
<td>2.0kg/cm</td>
<td>1.4 kg/cm</td>
</tr>
<tr align="center">
<td>Speed</td>
<td>0.11s</td>
<td>0.1S</td>
</tr>
</table>
</div>

## 2023/04/24 ~ 2023/04/30
**Member:**  ZHAO,ZHEN-BO、LIN,JHONG-BIN、HU,YUN-RUEI  
**Content:**  

- When the vehicle is uncertain about the distance ahead, it may fail to turn in time when it encounters a wall. To address this issue, ultrasonic sensors have been incorporated to allow the vehicle to initiate a turn before coming into contact with the wall.
- Based on the conducted experiments, it has been determined that ultrasonic sensors are only capable of detecting obstacles directly in front of the vehicle. Moreover, their effectiveness diminishes when the vehicle sways from side to side. Therefore, the decision has been made to implement a 360-degree LiDAR sensor. This sensor will not only detect distances in front of the vehicle but also on its left and right sides.

#### Distance Sensor
<div align="center" width=100%>
<table>
<tr align="center">
  <th>Ultrasound </th> 
  <th>Ydlidar x2</th>
</tr>
<tr>
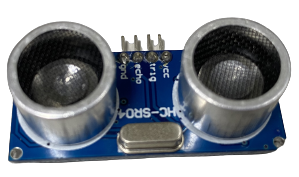
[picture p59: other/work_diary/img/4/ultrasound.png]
ultrasound
  <td></td>
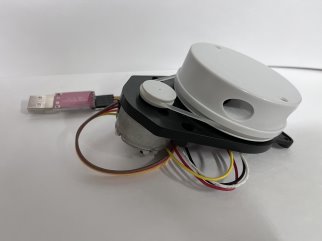
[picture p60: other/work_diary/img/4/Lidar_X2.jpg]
ydlidar x2
  <td>
  </td>
  </tr>
</table>
</div>

## 2023/05/01~ 2023/05/07  
**Member:**  ZHAO,ZHEN-BO、LIN,JHONG-BIN、HU,YUN-RUEI  
**Content:**  
- We began assembling the machine by using LEGO parts from the club to build the base. We then attached the motors, Raspberry Pi, and other components onto the chassis, making the machine functional.

   After the vehicle becomes operational, we further add additional sensors to enable the vehicle to sense its surroundings and respond accordingly based on mission requirements
- During testing, we discovered that the vehicle's movement speed using LEGO bricks was not fast, and its weight caused difficulties during turns. Consequently, we opted to use a laser cutting machine to cut wooden boards for the chassis, reducing the vehicle's weight, increasing its speed, and conserving power. Additionally, the use of wooden boards offers the advantage of adjusting dimensions and positions as needed. This adjustment is facilitated through tools like Onshape, allowing for flexible design and modifications without the need for constant adaptations like those required with LEGO in various scenarios."

<div align="center" width=100%>
<table>
<tr align="center">
  <th>Wooden boards</th>
  <th>Onshape web page</th>
  </tr>
<tr align="center">
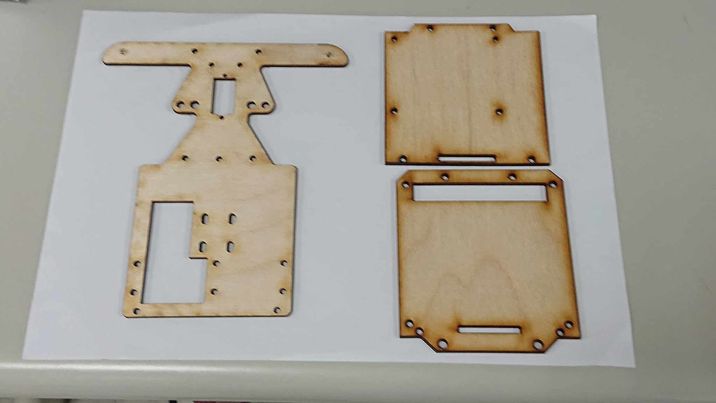
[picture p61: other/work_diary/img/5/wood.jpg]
wood
  <td>  </td>
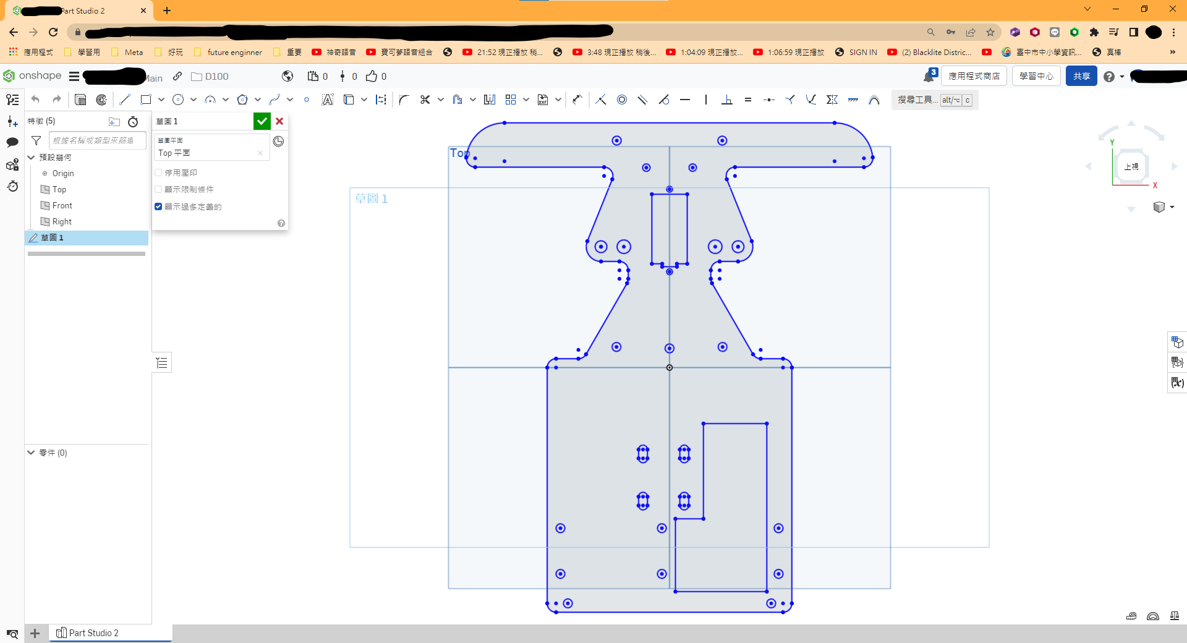
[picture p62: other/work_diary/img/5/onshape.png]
onshape
  <td>
  </td>
  </tr>
</table>
</div>

## 2023/05/08 ~ 2023/05/14  
**Member:**  ZHAO,ZHEN-BO、LIN,JHONG-BIN、HU,YUN-RUEI  
**Content:**  

- While it's feasible to move in a straight line and execute turns using the ultrasonic sensor, there's a risk of scraping against walls and encountering difficulties at corners. To address this, we substituted the ultrasonic sensor with a lidar, capable of detecting surroundings and maintaining the robot's position at the center of the path. Additionally, the lidar facilitates the identification of upcoming turns.
- Nevertheless, during actual testing of the YDLIDAR X4 and DLIDAR X2, we encountered a problem with missing angles (as depicted in the attached image). Therefore, for this competition, we opted to employ the D100 sensor for vehicle detection and measuring distances to side walls. The results yielded by the D100 sensor aligned with our expectations and requirements.

<div align="center" width=100%>
<table>
<tr align="center" >
  <th>Ydlidar x4</th> 
  <th>Ydlidar x2</th>
  <th>Lidar 100</th>
</tr>
<tr align="center">
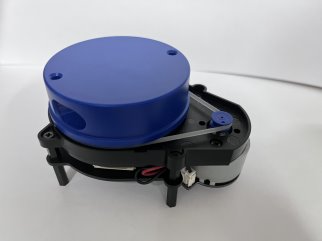
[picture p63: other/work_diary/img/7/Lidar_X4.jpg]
  <td></td>
  <td>Ydlidar x2</td>
  <td>Ydlidar x4</td>
</tr>
</table>
</div>

<div align="center" width=100%>
<table>
<tr align="center">
  <th colspan="2">Ydlidar x4、X2 distance imaging</th> 
  <th>Lidar 100 distance imaging</th>
</tr>
<tr align="center">
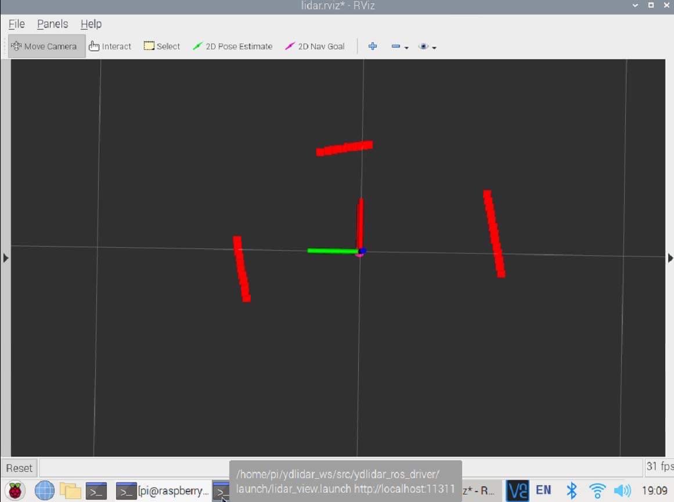
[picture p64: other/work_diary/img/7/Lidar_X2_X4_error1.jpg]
  <td></td>
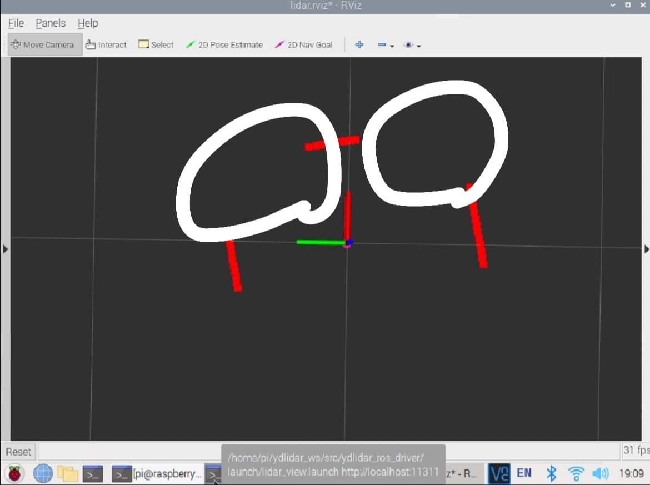
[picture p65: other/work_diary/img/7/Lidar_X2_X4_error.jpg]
  <td></td>
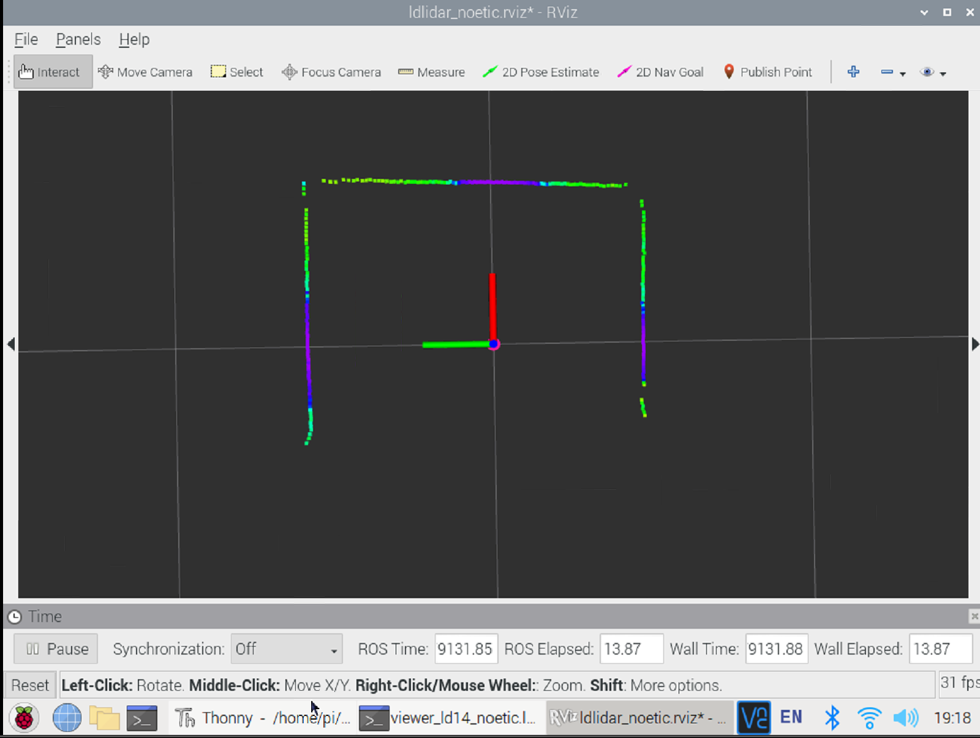
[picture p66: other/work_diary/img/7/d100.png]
D100
  <td>   
  </td>
  </tr>
</table>
</div>

## 2023/05/15 ~ 2023/05/21  
**Member:**  ZHAO,ZHEN-BO、LIN,JHONG-BIN、HU,YUN-RUEI  
**Content:**  
- TCS34725 color sensor 
  - In the competition, vehicles need to showcase more functionalities than just being able to turn. Merely knowing how to turn is insufficient. To achieve clockwise and counterclockwise turns, we must enable the vehicle to sense the color of lines on the ground and make appropriate judgments accordingly. Therefore, when selecting color sensors, we need to exercise special caution.
  - The TCS34725 color sensor has been chosen because it fulfills all the requirements of this competition. Firstly, it boasts exceptional sensing capabilities, enabling it to swiftly and accurately identify the colors of the ground lines. Secondly, the sensor is slim and compact, allowing it to be positioned near the ground without disrupting the vehicle's movements.
  - The high precision of this sensor ensures that the vehicle can accurately detect the colors of the ground lines and perform clockwise or counterclockwise turns as required. This is a crucial factor in the vehicle's excellent performance and its victory in the competition.

     In conclusion, the TCS34725 color sensor is a perfect fit for the requirements of this competition. Its slim design and highly accurate color recognition capabilities enable the vehicle to adapt flexibly to changes in ground lines, achieve clockwise and counterclockwise turns, and enhance its performance in the competition.

     I encountered a bottleneck when using the color sensor to detect lines because I was unsure how to write a Python program to detect the values of blue and orange lines. With the guidance of my teacher, I successfully overcame this challenge. The partial code is as follows:
- Additionally, during the implementation testing, we discovered that the original use of a USB 180-degree adapter (as shown in the lower left image) was prone to colliding with obstacles, particularly building blocks. As a result, we made a change and switched to using a USB 3.0 90-degree adapter for the connection. This modification reduces the likelihood of accidentally hitting obstacles while attempting to avoid them.

<div align="center" width=100%>
<table >
<tr align="center">
  <th>Snippet of Code</th> 
  <th>Function</th>
</tr>
<tr align="center">
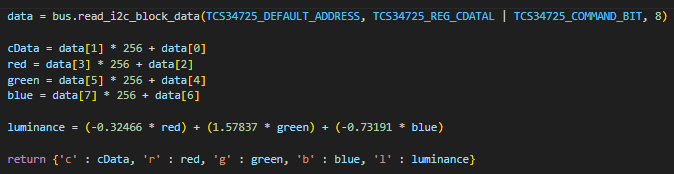
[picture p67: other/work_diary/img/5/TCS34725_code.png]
  <td> </td>
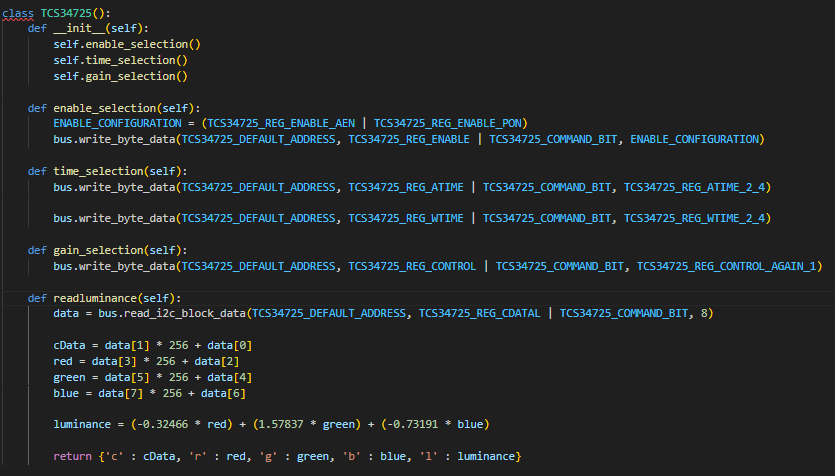
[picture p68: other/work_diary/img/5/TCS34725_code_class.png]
  <td>
  </td>  
  </tr>
</table>
</div>

<div align="center" width=100%>
<table >
<tr align="center">
  <th>USB Horizontal 180°</th> 
  <th>USB Vertical 90°</th>
</tr>
<tr align="center">
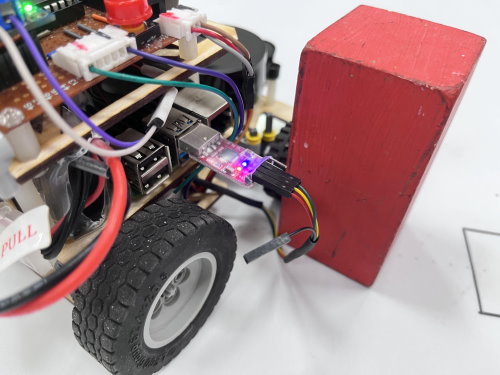
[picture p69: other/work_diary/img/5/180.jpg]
USB180
  <td align="center"></td> 
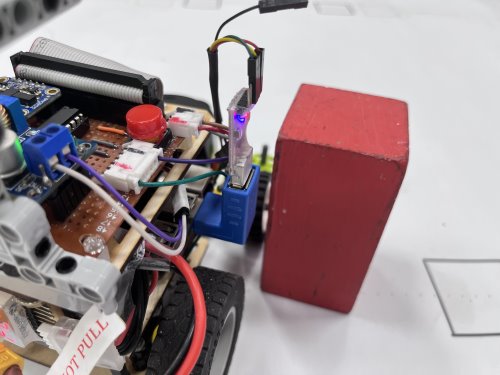
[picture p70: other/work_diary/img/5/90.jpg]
USB90
  <td align="center"></td>
</tr>
</table>
</div>

<div align="center" width=100%>
<table >
<tr align="center">
  <th >Event Photo</th> 
  <th >Event Photo</th> 
</tr>
<tr>
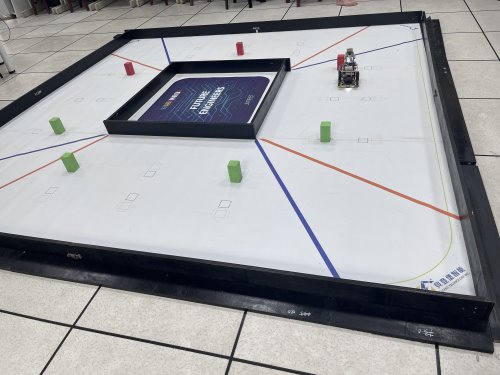
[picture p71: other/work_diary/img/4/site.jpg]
site
  <td align="center"></td> 
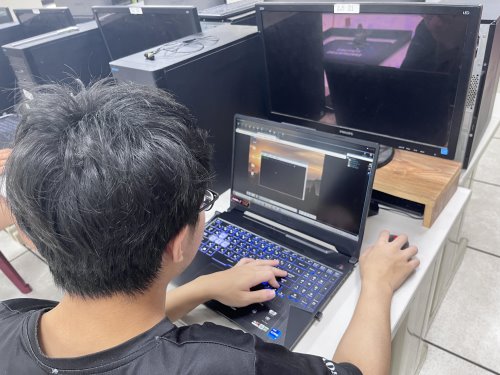
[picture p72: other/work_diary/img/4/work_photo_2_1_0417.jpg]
work_photo_2_1_0417
  <td align="center"></td>
</tr>
</table>
</div>

## 2023/05/22 ~ 2023/05/28  
**Member:**  ZHAO,ZHEN-BO、LIN,JHONG-BIN、HU,YUN-RUEI  
**Content:**  

- In order to enable the vehicle to avoid obstacles accurately, we need to install a camera module on the vehicle. Since we are using a Raspberry Pi as the controller, we need to find a compatible camera module for it. To do this, we referred to the camera module used by the American team in last year's competition and compared it with other camera modules in the same series. Here is the product information:

1. raspberry pi camera Rev 1.3(Sensor:OmniVision OV5647)
2. raspberry pi camera Module V2(Sensor:Sony IMX219)
3. raspberry pi camera Module V3(Sensor:Sony IMX708)

- Considering that V3 is not compatible with our existing Raspberry Pi operating system, we decided not to use that version. Additionally, the detection rate of version 1.3 is only 30p, whereas the V2 version can reach a maximum of 90p. Therefore, we ultimately chose the Raspberry Pi Camera Module V2 for our project. Through experimentation, we found that the V2 version has the best recognition performance.

#### Camera Module
<div align="center">
<table>
<tr  align="center">
<th rowspan="2">Model(model number)</td> 
<th>Raspberry pi camera Rev 1.3</th>
<th >Raspberry pi camera Module V2</th>
<th >Raspberry pi camera Module V3</th>
</tr>
<tr  align="center">
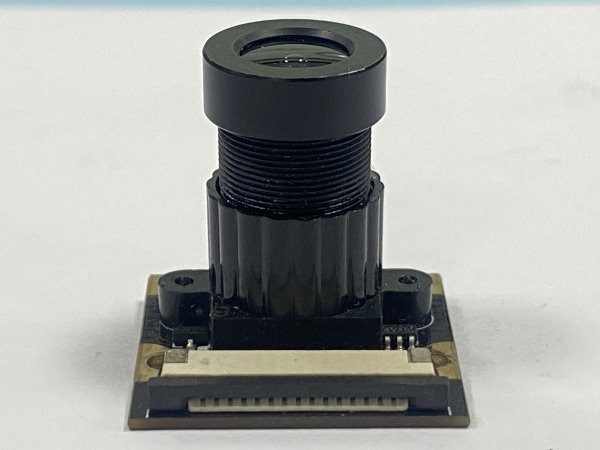
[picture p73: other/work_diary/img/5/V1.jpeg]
V1
<td ></td>
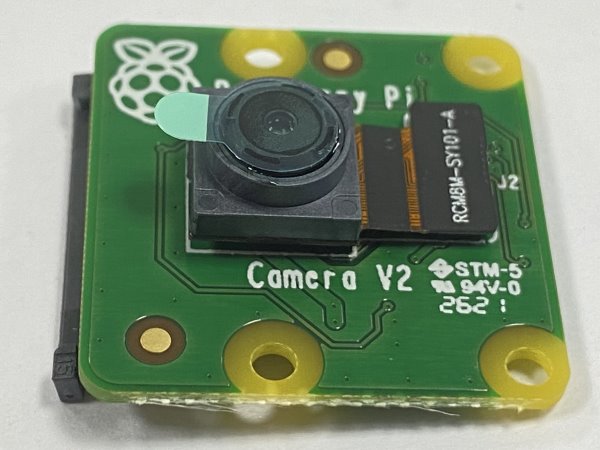
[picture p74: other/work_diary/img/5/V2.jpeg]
V2
<td ></td>
<td >V3</td>
</tr>
<tr  align="center">
<td>Sensor</td>
<td>Omnivision OV547</td>
<td >Sony IMX 219</td>
<td>Sony IMX 708</td>
</tr>
<tr  align="center">
<td>Sensor resolution</td>
<td >2592 * 1944 pix</td>
<td>3280 * 2464 pix</td>
<td>4608 * 2592 pix</td>
</tr>
<tr  align="center">  
<td>FPS Frame rate</td>
<td>60p MAX</td>
<td>90p MAX</td>
<td>120p MAX</td>
</tr>
</table>
</div>

During subsequent testing, we discovered that the vehicle was unable to predict the position of the next block while avoiding obstacles. This posed a challenge to the vehicle's obstacle avoidance strategy. Consequently, we decided to modify the original camera by converting it into a wide-angle lens. In comparison to the original 72-degree field of view, the wide-angle lens offers a 160-degree field of view, enabling us to anticipate the next block's position in advance. This enhancement has significantly improved the vehicle's obstacle avoidance effectiveness.

#### Wide-angle lens
<div align="center">
<table>
<tr>
<th align="center"> Without the wide-angle lens </th> 
<th align="center">With the wide-angle lens </th>
</tr>
<tr>
<td align="center">common</td><td>
wide angle
</td>
</tr>
<td align="center">common view</td>
<td align="center"> wide angle view</td>
</tr>
</table>
</div>

- In the Raspberry Pi program, it is possible to configure the resolution of the camera module. We conducted experiments with the following common resolutions.

  1. 1080x640 Frame rate30p
  
  2. 640x320 Frame rate60p
 
  3. 320x240 Frame rate90p
- In our experiments, we found that when the camera module's resolution was set to 1080x640, the high-resolution image processing demands led to a significant amount of time being spent on block recognition, resulting in a decrease in computational efficiency. On the other hand, when the resolution was set to 320x240, the computational efficiency was extremely high, but the low resolution hindered the proper recognition of the blocks. However, when we set the resolution to 640x320, we observed that the program could successfully recognize the blocks without compromising computational efficiency, thus avoiding collisions with the blocks. Therefore, we ultimately decided to set the camera module's resolution to 640x320.

## 2023/05/29 ~ 2023/06/04  
**Member:**  ZHAO,ZHEN-BO、LIN,JHONG-BIN、HU,YUN-RUEI  
**Content:**  

- By using VS Code along with Git to edit our technical documentation, we can effectively manage potential conflicts and improve collaboration. The advantages of this approach include easy version control, immediate notifications to editors when conflicts arise due to simultaneous edits, and the ability for editors who upload data later to merge conflicts by comparing the data. This way, we can ensure a smoother and more efficient process when working on the technical documentation.

[github Homepage ](https://github.com/kirkhu/WRO2023_FE-Shinan-Fire-On-All-Cylinders/tree/main)

<div align="center">
<table>
<tr align="center">
<th> To edit in VS Code, just click on the source file control and then press "Copy to Repository
</th> 
<th>Entering the URL allows you to perform editing and version control in VS Code
</th>
</tr>
<tr>
<td align="center">clone</td><td>
WEB
</td>
</tr>
</table>
</div>

## 2023/06/05 ~ 2023/06/11 
**Member:**  ZHAO,ZHEN-BO、LIN,JHONG-BIN、HU,YUN-RUEI  
**Content:**  

- During the hardware design process, we encountered a few instances in which the Raspberry Pi controller or IC was damaged due to incorrect power or data cable connections. To prevent such issues, we implemented a solution that involves using male-female connectors for both power supply and data transmission. This approach ensured proper wiring and effectively mitigated the risk of the Raspberry Pi or IC becoming damaged. These design improvements have enhanced the stability of the hardware system, leading to increased overall product reliability and lifespan.
- During the hardware design process, we initially used a breadboard to connect the circuits. Unfortunately, we encountered instances of burning or poor contacts, resulting in abnormal functionality or potential issues that were challenging to detect. To improve this situation, we made the decision to switch to soldering the circuits onto a prototyping board. This change significantly reduced the risks of burning or poor contacts while ensuring stable and reliable connections. Through this improvement, we successfully enhanced the overall hardware system's reliability and ensured proper functionality.

<div align="center">
<table>
<tr  align="center">
<th> 插座</th> 
<th>電木板</th>
</tr>
</table>
</div>

## 2023/06/12 ~ 2023/06/18
**Member:**  ZHAO,ZHEN-BO、LIN,JHONG-BIN、HU,YUN-RUEI  
**Content:**  

- Before dodging the blocks, we need to complete the basic task of circling the track three times. During this circling process, we noticed the possibility of the vehicle rubbing against the walls while turning. To address this, we utilize the 360-degree detection capability of LiDAR to keep the vehicle centered on the track. By subtracting the distances on the left and right sides, we obtain an error value, which is then corrected using the servo motor to ensure the vehicle continues to travel along the center of the track.

<div align="center">
<table>
<tr  align="center">
<th>The vehicle collides with the side wall.
</th> 
<th>Detecting the distance to the left and right walls.
</th>
</tr>
<tr align="center">
<td>hit wall</td>
<td>Distance to wall.</td>
</tr>
</table>
</div>

## 2023/06/19 ~ 2023/06/25   
**Member:**  ZHAO,ZHEN-BO、LIN,JHONG-BIN、HU,YUN-RUEI  
**Content:**  

- The vehicle is now able to operate successfully. The next step involves using the camera to avoid obstacles (blocks). Next, we need to detect the distance to the obstacles (blocks) and then identify the color of the blocks. By utilizing the features of OpenCV, we can calculate the distance between the blocks and the vehicle for obstacle avoidance. Through the implementation of an algorithm, we can control the front wheels to steer around these obstacles.
- However, there is an issue at the corners where the vehicle cannot avoid obstacles in a timely manner. To address this, we need to combine the gyroscope's readings with the output values from the algorithm to successfully navigate around corners.

<div align="center">
<table>
<tr align="center">
<th> Detecting block distance
</th> 
<th> Hitting a block
</th>
</tr>
<tr align="center">
<td>block distance</td>
<td>hit block
</td>
</table>
</div>

## 2023/06/26 ~ 2023/07/02 
**Member:**  ZHAO,ZHEN-BO、LIN,JHONG-BIN、HU,YUN-RUEI  
**Content:**  

- During today's testing, we discovered that the robot tends to misinterpret people wearing red or green clothing in its surroundings as obstacles. This misinterpretation leads it to avoid these individuals unnecessarily, which could potentially result in missing the opportunity to timely avoid the next block. To rectify this issue, we introduced an additional layer of black masking at the top of the camera's field of view. This measure effectively prevents the robot from detecting colors outside of the designated track area. With the implementation of this black masking, the robot will no longer register colors beyond the track area, thus minimizing the likelihood of interference.

<div align="center">
<table>
<tr align="center">
<th>Using a black mask to block colors from outside the field.
</th> 
</tr>
<tr align="center">
<td>cover</td>
</table>
</div>

## 2023/07/03 ~ 2023/07/09 
**Member:**  ZHAO,ZHEN-BO、LIN,JHONG-BIN、HU,YUN-RUEI  
**Content:**  

- This week, most of the programming has been completed, and we began testing the robot's success rate. We started with a speed of 50%, and due to its slower pace, the robot responded well for the most part. However, when accelerating to 70% speed, the color sensor occasionally misjudged the track's color due to its high speed. As a result, we modified the turning conditions to use the LiDAR's measurements of the left and right directions for determining the turning direction. This adjustment reduces the likelihood of turning in the wrong direction because of color misjudgment.

#### Detecting the direction of the turn
```
if get_left_dis > 100:
    reverse = False
else:
    reverse = True
if get_mid_dis > 55:
    servo.angle(-40)
```

## 2023/07/10 ~ 2023/07/16 
**Member:**  ZHAO,ZHEN-BO、LIN,JHONG-BIN、HU,YUN-RUEI  
**Content:**  

- The vehicle is now capable of successfully avoiding obstacles and completing the third lap around the track. The next task is to detect blocks and perform a turnaround maneuver. The turnaround will be executed only if the last block of the second lap is red. Therefore, it is necessary to detect the number of laps. We will use the color sensor to count the number of times the line is crossed and determine whether the set count has been reached.

- If the specified count has not yet been achieved, the system will continue to record the color of the nearest traffic sign until the count of line crossings is greater than or equal to the set count. At this point, the color recording will cease.

- After recording the color of the nearest traffic sign, the program will determine whether the color is red. If the color is indeed red, the system will adjust the angle of the servo motor to initiate a right turn and will continue turning until the vehicle is properly aligned in the specified direction, thus executing a turnaround maneuver. If the detected color is not red, the vehicle will proceed to move forward.

<div align="center">
<table>
<tr align="center">
<th>Display the number of line crossings and <br>the color of the nearest traffic sign.</th>
<th>Adjusting the values.
</th>
</tr>
<tr align="center">
<td>print color</td>
<td>check</td>
</table>
</div>

## 2023/07/17 ~ 2023/07/23  
**Member:**  ZHAO,ZHEN-BO、LIN,JHONG-BIN、HU,YUN-RUEI  
**Content:**  

- As the field mission has been roughly completed, we are going to start writing the technical report. Since we are not familiar with the correct technical report format, we have referred to the official website's technical report documentation and found that the report should include the following sections.

  1. modles: This folder should contain documentation related to the vehicle models, such as files for laser cutting machines and 3D printers.

  2. other: This folder is used to store data that does not belong to other categories, such as communication protocols and engineering logs.

  3. schemes: This folder is dedicated to hardware introductions, explaining the functions of electronic components and how they are connected.

  4. src: All programs should be placed in this folder.

  5. t-photos: This folder should contain team photos, including a group photo and funny pictures.

  6. v-photos: Machine photos from six different perspectives should be placed in this folder.

  7. video: Videos demonstrating the machine's operation should be placed in this folder, with each video lasting more than 30 seconds.

- When writing the technical report, we are switching between VS Code and the GitHub website. We use a desktop computer to view the GitHub web page and a laptop to edit the report in VS Code.

<div align="center">
<table>
<tr align="center">
<th>Official website's GitHub example</th> 
<th>Laptop and desktop comparison and modifications</th>
</tr>
<tr align="center">
<td>github_example</td>
<td>更改文件</td>
</table>
</div>

## 2023/07/24 ~ 2023/07/30  
**Member:**  ZHAO,ZHEN-BO、LIN,JHONG-BIN、HU,YUN-RUEI  
**Content:**  

- We organized and listed the components in the parts inventory, and we uploaded them to the technical documentation.Additionally, we completed the drawing of the vehicle's introduction diagram. Throughout this process, we embarked on a learning journey, gradually familiarizing ourselves with GitHub syntax. Although we are not yet fully proficient in using GitHub, we dedicated time to researching relevant information online and steadily improving our skills. These achievements have brought valuable advancements to our report and project as a whole.
- Over the past few days, we have been continuously adjusting and fine-tuning the execution of the tasks at the venue, making constant adjustments to motor speed and various parameters, with the hope of effectively reducing the error rate. We are eager to achieve better performance and improve our overall competition results.
- During practical testing, we discovered that the vehicle was getting stuck at the junctions of the terrain due to protrusions, which was affecting its normal operation. To address this issue, we adopted a method of using a laser cutting machine to create 3mm thick spacers. These spacers were then placed under the vehicle chassis to elevate its height, enabling the vehicle to pass over the obstacles smoothly.

#### Overcoming Terrain Protrusions 

<div align="center">
<table>
<tr align="center">
<th> Spacer</th> 
<th>Spacer</th>
<th>Spacer</th>
</tr>
<tr align="center">
<td>Spacer</td>
<td>Spacer</td>
<td>Spacer</td>
</table>
</div>

### Team Members' Practice Status

<div align="center">
<table>
<tr  align="center"> 
<th> work_photo_2_1_0729</th> 
<th>work_photo_2_2_0729</th>
</tr>
<tr align="center">
<td>work_photo_1_1_0727</td>
<td>work_photo_2__0727</td>
</tr>
</table>
</div> 

## 2023/07/31 ~ 2023/08/06
**Member:**  ZHAO,ZHEN-BO、LIN,JHONG-BIN、HU,YUN-RUEI  
**Content:**   

- As the deadline for submitting the technical report is next week, we have begun revising the content of the technical documentation. We are also adjusting the website according to the official grading criteria and continuously adding to the technical report.
- Complete recording videos for each task and upload them to YouTube.

<table>
<tr align="center">
<th> Old directory </th>
<th> Revised Directory (Upper Section) </th>
<th> Revised Directory (Lower Section) </th>
</tr>
<tr align="center">
<td>old_content </td>
<td> new1_content</td>
<td> new1_content</td>
</tr>
</table>

  __Open Challenge__
  - [Open Challenge full narrow speed 70%](https://youtu.be/QtpuHt05MDg)
  - [Open Challenge full anrrow speed 50%](https://youtu.be/QaYUrrdAtE8)
  - [Open Challenge half width and half narrow speed 70%](https://youtu.be/pcTpH8QgJFU)
  - [Open Challenge half width and half narrow speed 50%](https://youtu.be/7HdWxfWPfWc)
  - [Open Challenge all width speed 70%](https://youtu.be/MA1k2P87LdE)
  - [Open Challenge all Width speed 50%](https://youtu.be/OUg0x4Qdc0c)  

 __Open Challenge__
  - [Obstacle Challenge speed 50% ](https://youtu.be/Jo7555gfXG8)
  - [Obstacle Challenge speed 70% ](https://youtu.be/iCmcXbACizY)

__Team Members' Practice Status__

<div align="center">
<table>
<tr align="center">
<th>Report writing</th> 
<th>Mechanism adjustment</th>
<th>Report writing</th>
<th>Field mission practice</th>
</tr>
<tr align="center">
<td>work_daily</td>
<td>work_daily</td>
<td>work_daily</td>
<td>work_daily</td>
</table>
</div>

## 2023/08/07 ~ 2023/08/13
**Member:**  ZHAO,ZHEN-BO、LIN,JHONG-BIN、HU,YUN-RUEI  
**Content:**  

- This week, with our machine now adjusted to smoothly complete the mission race on the field, we have begun filming an introductory video for the race. In the video, we will showcase the actions our vehicle performs during the mission race, providing explanations through subtitles synchronized with the video.

<div align="center">
<table>
<tr align="center">
<th>Modifying code and testing vehicles</th>
<th>Currently editing videos</th>
</tr><tr align="center">
<td>work_daily</td>
<td>work_daily</td>
</tr><tr align="center">
</table>

<table>
<th>Mission race introduction video</th>
</tr>
<td>

video (https://youtu.be/EAkR-t_6i7g "video")</td>
</table>
</div>

## 2023/08/14 ~ 2023/08/20
**Member:**  ZHAO,ZHEN-BO、LIN,JHONG-BIN、HU,YUN-RUEI  
**Content:**  

- As the competition is scheduled for this week, we have intensified our practice efforts, trying out various scenarios and adjusting our program to adapt to a wide range of situations. Experimenting with different scenarios has the advantage of helping us anticipate challenges that our machine might face and making necessary adjustments in advance. Here's our practice approach:

- We have assigned lane labels A, B, C, and D. Each lane is divided into three sections, with placement points for blocks both on the inner and outer sides in each section. Red blocks indicating turning conditions will be placed sequentially, while the positions of other blocks will be randomized.
- The record sheet will include the following information:
  1. Completion time
  2. Number of successful attempts/number of failed attempts
We believe that this approach will assist our machine in preparing for a variety of scenarios, ensuring that we are well-prepared for the competition.

- Today is 8/19, our match day. In the first half of the qualifying round, due to our Request for Maintenance during the initial round, the score was reduced by 50%, resulting in our obtaining 15 points. In the second round, we successfully completed it and achieved a full score of 30 points, allowing us to advance to the second half of the obstacle course. During the first obstacle race, our robot hit the wall and stopped due to excessive avoidance; fortunately, after adjustments, the second attempt by our team resulted in a perfect score. This marked a successful conclusion to today's competition.

<div align="center">
<table>
<tr align="center">
<th>Field layout</th>
<th>Record sheet</th> 
</tr>
<tr align="center">
<td>work_daily</td>
<td>work_daily</td>
</table>
</div>
<div align="center">
<table>
<tr align="center">
<th>Competition photos</th>
<th>Award-winning photo</th> 
</tr>
<tr align="center">
<td>contest</td>
<td>award-winning photo</td>
</table>
</div>

## 2023/08/21 ~ 2023/08/27
**Member:**  ZHAO,ZHEN-BO、LIN,JHONG-BIN、HU,YUN-RUEI  
**Content:**  

- As we have confirmed our participation in the international competition, we are undergoing significant modifications to our vehicle. Moreover, this redesign will allow us to incorporate threaded components for added stability. Additionally, we are upgrading the controller from Raspberry Pi 4B to the higher computing power provided by the Jetson Nano microcomputer. The Jetson Nano supports programming in Python, thus most of our existing code does not need significant modifications. However, one notable difference with the Jetson Nano is that the generation of PWM signals requires an external board for implementation.

- After switching to Jetson Nano, we encountered issues with the Camera V2. After some investigation, we discovered that V2 and V3 cameras are designed for use with Raspberry Pi. So, we decided to switch to the IMX 219-160 camera, which is compatible with Jetson Nano. This camera comes with a wide-angle lens, eliminating the need for modifications.

<div align="center">
<table>
<tr align="center">
<td rowspan="2">Controller</td>
<td>Jetson Nano</td>
<td>Raspberry Pi 4B</td>
<tr align="center">
<td>work_daily</td>
<td>work_daily</td>
</tr>
<tr align="center">
<td>Computational efficiency</td>
<td>472 GFLOPs</td>
<td>13.5 GFLOPs</td>
</table>
</div>

<div align=center>
<table>
<tr align=center>
<th>160 width-angle</th>
</tr><tr>
<td>work_daily</td>
</tr>
</table>
</div>

<small>Data source:</small>  
<small>[Taiwansersor](https://www.taiwansensor.com.tw/product/nvidia-jetson-nano-developer-kit-%E4%BA%BA%E5%B7%A5%E6%99%BA%E6%85%A7%E9%96%8B%E7%99%BC%E5%A5%97%E4%BB%B6-ai-%E9%96%8B%E7%99%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)</small>  
<small>[University of Maine System](https://web.eece.maine.edu/~vweaver/group/green_machines.html)</small>

## 2023/08/28 ~ 2023/09/03
**Member:**  ZHAO,ZHEN-BO、LIN,JHONG-BIN、HU,YUN-RUEI  
**Content:**  
Today, we started learning how to use the stereolithography 3D printer and how to maintain it after printing. Our senior demonstrated the process to us. Here are the maintenance steps:

1. After printing is complete, the finished product will be stuck to the build plate.
2. Remove the build plate and wipe off the resin, being careful not to touch the finished product.
3. Rinse off easily removable supports with water.
4. Spray alcohol onto the finished product, making sure to reach every corner.
5. Wipe the finished product to remove excess resin.
6. Carefully detach the finished product using tools.
7. Use a knife to scrape away any remaining support material on the finished product.
8. Rinse off any fine residue with water.
9. Wipe the build plate clean of resin, and it's ready for the next print.

<div align="center">
<table>
<tr align="center">
<td>work_daily</td>
<td>work_daily</td> 
<td>work_daily</td>
</tr>
<tr align="center">
<td>work_daily</td>
<td>work_daily</td>
<td>work_daily</td>
</tr>
<tr>
<td>work_daily</td>
<td>work_daily</td>
<td>work_daily</td>
</tr>
</table>
</div>

## 2023/09/04 ~ 2023/09/10
**Member:**  ZHAO,ZHEN-BO、LIN,JHONG-BIN、HU,YUN-RUEI  
**Content:**  

- Today, we utilized a stereolithography 3D printer to produce the fixtures for our front steering mechanism, allowing us to optimize the space utilization of the steering mechanism. We chose stereolithography due to its advantages, such as a smooth surface finish, high precision, and easy maintenance. However, it's worth noting that this method tends to have longer print times. Consequently, we exclusively used it for components that needed to be printed separately, like the Ackermann steering mechanism and the bearing mounting bracket. This approach not only saved printing time but also ensured high precision in the components.

- This week, our club acquired a stacked 3D printer, which means we can now start working on vehicle integration. One of the advantages of using a 3D printer is that we can create threads, which allows for more secure fastening of screws. With vehicle integration, we can reduce the overall size, making the machine more lightweight.

- Earlier, we had multiple failed attempts at printing, and we discovered that it was because we weren't using supports. Since the printer works by stacking layers on top of each other, any overhanging parts without support would collapse. When we removed the finished prints, they would often break. After realizing that the infill density was too low, resulting in fragile prints, we increased the density, which helped us successfully complete the prints.

- When assembling the vehicle, we found that the photopolymer parts remained soft and were prone to deformation. Therefore, we used ultraviolet (UV) light for secondary curing to make the parts less susceptible to deformation.

<div align="center">
<table>
<tr align="center">
<th>Maintenance of Photocuring 3D Printer</th>
<th colspan="3">Finished Product Photos</th> 
</tr>
<tr align="center">
<td>work_daily</td>
<td>work_daily</td>
<td>work_daily</td>
<td>work_daily</td>
</tr>
</table>
</div>

<div align=center>
<table>
<tr align=center>
<th>3D Printer</th>
<th>3D Printer working</th>
</tr><tr align=center>
<td>3D printer</td>
<td>3D printer</td>
</tr>
</table>
</div>

#### 3D printed product
<div align="center">
<table>
<tr  align="center"> 
<td>work_photo_2_1_0729</td> 
<td>work_photo_2_2_0729</td>
</tr>
</table>
</div>

<div align=center>
<table>
<tr>
<th>Secondary curing</th>
</tr><tr>
<td>light_again</td>
</tr>
</table>
</div>

## 2023/09/11 ~ 2023/09/17
**Member:** ZHAO,ZHEN-BO、LIN,JHONG-BIN、Hu,Yun-Ruei  
**Content:**

This week, we started modifying the program. Due to the differences in the Raspberry Pi and Jetson Nano environments, even though both use Python, we had to make significant changes to the program. With the modifications to the vehicle and the circuitry, there were many areas in the code that required adjustments. We faced several challenges during the qualifying rounds, such as the LiDAR not detecting obstacles properly, the battery slipping can get stuck in the tire, and the light sensor being too sensitive, among other issues.

While the 3D-printed chassis offered advantages such as size reduction and greater flexibility, it was not sturdy enough and prone to breaking. Therefore, we ultimately decided to use a laser cutting machine to cut wooden boards for the chassis.

During vehicle testing, we discovered that the Jetson Nano's reading speed for the color sensor was extremely slow, leading to difficulties in the vehicle's turning accuracy. When we switched back to the Raspberry Pi, the reading speed returned to normal. Later, we realized that while the Jetson Nano has extremely fast image recognition capabilities, it consumes a significant amount of processing power for this task. Additionally, the I2C interface is used not only for the color sensor but also for the motor controller and PWM controller, which contributed to the decision to switch the main controller back to the Raspberry Pi 4B.

<div align="center">
<table>
<tr  align="center"> 
<td>work_photo_2_2_0729</td>
<td>work_photo_2_1_0729</td> 
</tr>
</table>
</div>

<div align="center">
<table>
<tr  align="center"> 
<td>work_photo_2_2_0729</td>
<td>work_photo_2_1_0729</td> 
</tr>
</table>
</div>

## 2023/09/18 ~ 2023/09/24
**Member:**  ZHAO,ZHEN-BO、LIN,JHONG-BIN、HU,YUN-RUEI  
**Content:**  

This week, we have completed assembling the machine and started practicing. Since there haven't been many changes to the program, the most challenging part is the turning at the starting area. We have set up a practice mode specifically for practicing turns. There are a total of 32 combinations, divided into clockwise and counterclockwise turns. The red pieces are placed in slots 1 and 2, and they alternate with green pieces in slots 3 to 6. This is to test if there are any collisions with the blocks or if the machine passes through them from the wrong direction during the turns. Each combination will be tested three times. The diagram and practice conditions are as follows:

<div align="center">
<table>
<tr>
<th>Record Sheet(Success Count / Practice Count)<br> </th>
<th>Clockwise Diagram (Black Arrow indicates the direction of movement) <br></th>
<th>Counterclockwise Diagram (Black Arrow indicates the direction of movement)<br></th>
</tr>
<tr  align="center"> 
<td>work_photo_2_2_0729</td>
<td>work_photo_2_1_0729</td> 
<td>work_photo_2_1_0729</td> 
</tr>
</table>
</div>

## 2023/09/25 ~ 2023/10/01
**Member:** ZHAO,ZHEN-BO、LIN,JHONG-BIN、Hu,Yun-Ruei  
**Content:**

In the testing process, we encountered a fracture on the chassis, which was found to be due to the servo motor's shaft not being centered, resulting in a shorter gap on one side when drilling holes in the base plate. This lack of stability caused the fracture. Therefore, we made adjustments to ensure that both sides have the same gap, increasing the chassis's overall rigidity.

<div align=center>
<table>
<tr>
<th>Original </th>
<th>Improved version </th>
</tr><tr align=center>
<td></td>
<td></td>
</tr>
</table>
</div>

## 2023/10/02 ~ 2023/10/08
**Member:** ZHAO,ZHEN-BO、LIN,JHONG-BIN、Hu,Yun-Ruei  
**Content:**

This week, our vehicle often had trouble making proper turns, and we later discovered that it was due to detecting the green blocks of the next section. This resulted in the last block being recorded as green, preventing it from making the turn. Afterward, we utilized the Y-axis to determine whether to record the blocks. Since our camera's coordinate system has (0,0) at the top-left corner, a higher Y-axis value indicates closer proximity. Thus, the condition for deciding whether to record the block is whether the block's Y-axis is greater than the set value. If this condition is met, we record the block's color; if not, we don't record it.

When the program is initiated, because the button is located on the circuit board and positioned beneath the camera, pressing the button without promptly retracting the hand could potentially interfere with the machine's operation. To address this issue, we have positioned the button on an extended wooden board, ensuring that even if the hand is not retracted in time, it will not disrupt the functioning of the vehicle.

<div align=center>
<table>
<tr align=center><th>Diagram</th>
<th>Original</th>
<th>Revised</th>
</tr>
<tr align=center><td></td>
<td></td>
<td></td>
</tr>
</table>
</div>

## 2023/10/09 ~ 2023/10/15
**Member:** ZHAO,ZHEN-BO、LIN,JHONG-BIN、Hu,Yun-Ruei  
**Content:**

This week, the hardware of the machine has been completed. Next, it's all about continuous practice, program modifications, and report writing. The report has numerous issues with both text and formatting, making it challenging to clearly distinguish the content to be expressed. Therefore, we are using an indented format to differentiate. When there are sub-items under a main item, the sub-items are indented by one level, which allows for a clear distinction of the content of different items.

## 2023/10/16 ~ 2023/10/22
**Member:** ZHAO,ZHEN-BO、LIN,JHONG-BIN、Hu,Yun-Ruei  
**Content:**

This week, we started making final adjustments. With only two weeks left before the competition, we started to speed up our work and began to write paper materials. We used PowerPoint to create them because PowerPoint allows for free layout, so we could fit all the necessary data into them. Although there was a lot of data, it could be well-organized through layout and would not be cluttered.

<div align="center">

</div>

# <div align="center">HOME[Return Home](../../)</div>

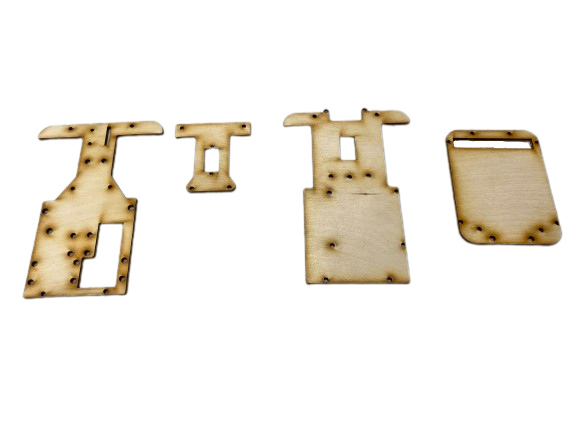
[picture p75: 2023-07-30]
other/work_diary/img/5/wood.png

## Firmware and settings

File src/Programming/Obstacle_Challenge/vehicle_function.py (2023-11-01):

#Import the required modules(匯入所需的模組)
import pigpio       #Raspberry Pi I/O Control Function Library
import time         #Time Module時間模組
import smbus        #I2C Manage
import struct       #Binary Data Packing and Unpacking Module二進位數據打包、解包的模組
import os           #System Information Reading Module 讀系統資訊
import math         #Mathematical Calculation Module 數學運算
import cv2          #OpenCV  Module 影像處理
import threading    #Multithread Management  Module 多執行緒管理
import pickle       #Serialization/Deserialization Module 序列化/反序列化模組
import rospy        #ROS Python Commands Module ROS的Python指令
import numpy as np  #Multidimensional Arrays and Matrix Operations Module 多維陣列與矩陣運算
import signal       #Exception Handling Module 異常事件處理模組
from sensor_msgs.msg import LaserScan  #ROS Data Structure Definitions ROS定義資料結構

#==========Pin configuration(腳位設定)==========
Red_LED_pin = 27   
Green_LED_pin = 22
Motor_IN1_pin = 6  
Motor_IN2_pin = 13 
Motor_PWM_pin = 19
Button_pin = 5    
Servo_pin = 26    
#==========Parameter Settings(參數設定)==========
servo_offset = 15                      
reverse = False 

# Servo Motor Angle Limitation(伺服馬達角度限制) 
servo_range = 30                  
block_detect_min_area = 100

#Black mask area at the top of the image screen(影像畫面上方黑色遮罩範圍)
image_black_area = 310

#Black mask area at the bottom of the image frame(影像畫面下方黑色遮罩範圍)
image_black_area_down = 400 

#Adjusting Image Brightness(影像畫面亮度調整)
camera_BRIGHTNESS = 55   
RADIAN_TO_DEGREES = 360/(math.pi *2)
pi = pigpio.pi()

def mapping(x, in_min, in_max, out_min, out_max):
    return (x - in_min) * (out_max - out_min) / (in_max - in_min) + out_min

def constrain(x, out_min, out_max):
    return out_min if x < out_min else out_max if x > out_max else x
# Get I2C bus
bus = smbus.SMBus(1)

# I2C Address of the device
TCS34725_DEFAULT_ADDRESS = 0x29

# TCS34725 Register Set
TCS34725_COMMAND_BIT = 0x80
TCS34725_REG_ENABLE = 0x00 # Enables states and interrupts
TCS34725_REG_ATIME = 0x01 # RGBC integration time
TCS34725_REG_WTIME = 0x03 # Wait time
TCS34725_REG_CONFIG = 0x0D # Configuration register
TCS34725_REG_CONTROL = 0x0F # Control register
TCS34725_REG_CDATAL = 0x14 # Clear/IR channel low data register
TCS34725_REG_CDATAH = 0x15 # Clear/IR channel high data register
TCS34725_REG_RDATAL = 0x16 # Red ADC low data register
TCS34725_REG_RDATAH = 0x17 # Red ADC high data register
TCS34725_REG_GDATAL = 0x18 # Green ADC low data register
TCS34725_REG_GDATAH = 0x19 # Green ADC high data register
TCS34725_REG_BDATAL = 0x1A # Blue ADC low data register
TCS34725_REG_BDATAH = 0x1B # Blue ADC high data register

# TCS34725 Enable Register Configuration
TCS34725_REG_ENABLE_SAI = 0x40 # Sleep After Interrupt
TCS34725_REG_ENABLE_AIEN = 0x10 # ALS Interrupt Enable
TCS34725_REG_ENABLE_WEN = 0x08 # Wait Enable
TCS34725_REG_ENABLE_AEN = 0x02 # ADC Enable
TCS34725_REG_ENABLE_PON = 0x01 # Power ON

# TCS34725 Time Register Configuration
TCS34725_REG_ATIME_2_4 = 0xFF # Atime = 2.4 ms, Cycles = 1
TCS34725_REG_ATIME_24 = 0xF6 # Atime = 24 ms, Cycles = 10
TCS34725_REG_ATIME_101 = 0xDB # Atime = 101 ms, Cycles = 42
TCS34725_REG_ATIME_154 = 0xC0 # Atime = 154 ms, Cycles = 64
TCS34725_REG_ATIME_700 = 0x00 # Atime = 700 ms, Cycles = 256
TCS34725_REG_WTIME_2_4 = 0xFF # Wtime = 2.4 ms
TCS34725_REG_WTIME_204 = 0xAB # Wtime = 204 ms
TCS34725_REG_WTIME_614 = 0x00 # Wtime = 614 ms

# TCS34725 Gain Configuration
TCS34725_REG_CONTROL_AGAIN_1 = 0x00 # 1x Gain
TCS34725_REG_CONTROL_AGAIN_4 = 0x01 # 4x Gain
TCS34725_REG_CONTROL_AGAIN_16 = 0x02 # 16x Gain
TCS34725_REG_CONTROL_AGAIN_60 = 0x03 # 60x Gain

#Executing threads for task scheduling(執行緒進行執行排程)
    def start(self):
        self.thread = True
        self.color_read_thread.start()
        self.camera_stream_thread.start()
	    
#Capture images(擷取影像)
    def camera_stream(self):
        while self.thread:
            _, self.raw_image = self.imcap.read()
            self.key = cv2.waitKey(15)

#Identify obstacle coordinates and calculate the center point of the obstacle(辨識障礙物座標並計算出障礙物中心點)        
    def color_detect(self,raw_img, hsv_img, lower, upper):
        mask = cv2.inRange(hsv_img, lower, upper)  
        contours, hierarchy = cv2.findContours(mask, cv2.RETR_TREE, cv2.CHAIN_APPROX_SIMPLE)
        find_x = -1
        find_y = -1
        max_y = 0
        find_area = 0
        for pic, contour in enumerate(contours):
            area = cv2.contourArea(contour)
            x, y, w, h = cv2.boundingRect(contour)
            x = int(x + w / 2)
            y = int(y + h / 2)
            if y > max_y and area > block_detect_min_area:
                find_area = area
                max_y = y
                find_x = x
                find_y = y
        return raw_img, find_x, find_y, find_area

#Calculate Program FPS(計算程式運算速度)
    def get_program_fps(self):
        return int(1 / self.program_fps)

#Read keyboard keys(讀取鍵盤按鍵)
    def get_keyboard(self):
        return self.key
#Return the variable green_x to allow external code to access this value(將變數green_x回傳，讓外部程式碼可以獲取該值)
    def get_green_x(self):
        return self.green_x

#Return the variable green_y to allow external code to access this value(將變數green_y回傳，讓外部程式碼可以獲取該值)
    def get_green_y(self):
        return self.green_y

#Return the variable green_area to allow external code to access this value(將變數green_area回傳，讓外部程式碼可以獲取該值)
    def get_green_area(self):
        return self.green_area

#Return the variable red_x to allow external code to access this value(將變數red_x回傳，讓外部程式碼可以獲取該值)
    def get_red_x(self):
        return self.red_x

#Return the variable red_y to allow external code to access this value(將變數red_y回傳，讓外部程式碼可以獲取該值)
    def get_red_y(self):
        return self.red_y
	    
#Return the variable red_area to allow external code to access this value(將變數red_area回傳，讓外部程式碼可以獲取該值)
    def get_red_area(self):
        return self.red_area

#Terminating a thread(將執行緒終止)
    def shutdown(self):
        self.thread = False
        self.color_read_thread.join()
        self.camera_stream_thread.join()
        self.imcap.release()

#Define a class for a color sensor(定義顏色感測器的類別)
class TCS34725():
    def __init__(self):
        self.enable_selection()
        self.time_selection()
        self.gain_selection()

    def enable_selection(self):
        """Select the ENABLE register configuration from the given provided values"""
        ENABLE_CONFIGURATION = (TCS34725_REG_ENABLE_AEN | TCS34725_REG_ENABLE_PON)
        bus.write_byte_data(TCS34725_DEFAULT_ADDRESS, TCS34725_REG_ENABLE | TCS34725_COMMAND_BIT, ENABLE_CONFIGURATION)

    def time_selection(self):
        """Select the ATIME register configuration from the given provided values"""
        bus.write_byte_data(TCS34725_DEFAULT_ADDRESS, TCS34725_REG_ATIME | TCS34725_COMMAND_BIT, TCS34725_REG_ATIME_2_4)

        """Select the WTIME register configuration from the given provided values"""
        bus.write_byte_data(TCS34725_DEFAULT_ADDRESS, TCS34725_REG_WTIME | TCS34725_COMMAND_BIT, TCS34725_REG_WTIME_2_4)

    def gain_selection(self):
        """Select the gain register configuration from the given provided values"""
        bus.write_byte_data(TCS34725_DEFAULT_ADDRESS, TCS34725_REG_CONTROL | TCS34725_COMMAND_BIT, TCS34725_REG_CONTROL_AGAIN_1)

    def readluminance(self):
        """Read data back from TCS34725_REG_CDATAL(0x94), 8 bytes, with TCS34725_COMMAND_BIT, (0x80)
        cData LSB, cData MSB, Red LSB, Red MSB, Green LSB, Green MSB, Blue LSB, Blue MSB"""
        data = bus.read_i2c_block_data(TCS34725_DEFAULT_ADDRESS, TCS34725_REG_CDATAL | TCS34725_COMMAND_BIT, 8)
        
        # Convert the data
        cData = data[1] * 256 + data[0]
        red = data[3] * 256 + data[2]
        green = data[5] * 256 + data[4]
        blue = data[7] * 256 + data[6]
        
# Calculate luminance
        luminance = (-0.32466 * red) + (1.57837 * green) + (-0.73191 * blue)

        return {'c' : cData, 'r' : red, 'g' : green, 'b' : blue, 'l' : luminance}

#Define a class for buttons(定義按鈕的類別)
class button_control():
    def __init__(self):
        pi.set_mode(Button_pin, pigpio.INPUT)
        pi.set_pull_up_down(Button_pin, pigpio.PUD_UP)

#Read button(讀取按鈕)
    def raw_value(self):
        return pi.read(Button_pin)

#Wait for the button until it's pressed(等待按鈕直到按下)	
    def wait_press(self):
        state = 1
        while state == 1:
            state = pi.read(Button_pin)

    def wait_press_release(self):
        button_state = 1
        while button_state == 1:
            button_state = pi.read(Button_pin)
        button_state = 0
        while button_state == 0:
            button_state = pi.read(Button_pin)

    def wait_release(self):
        state = 0
        while state == 0:
            state = pi.read(Button_pin)

#Define a class for LEDs(定義LED的類別)
class LED_control():
    def __init__(self):
        pi.set_mode(Red_LED_pin, pigpio.OUTPUT)
        pi.set_mode(Green_LED_pin, pigpio.OUTPUT)

#Turn on the green LED(打開綠色LED)
    def green_on(self):
        pi.write(Green_LED_pin, pigpio.HIGH)

#Turn off the green LED(關閉綠色LED)
    def green_off(self):
        pi.write(Green_LED_pin, pigpio.LOW)

#Turn on the red LED(打開紅色LED)
    def red_on(self):
        pi.write(Red_LED_pin, pigpio.HIGH)

#Turn off the red LED(關閉紅色LED)
    def red_off(self):
        pi.write(Red_LED_pin, pigpio.LOW)

#Define a class for DC motors(定義直流馬達的類別)
class dc_motor():
    def __init__(self):
        pi.set_mode(Motor_IN1_pin, pigpio.OUTPUT)
        pi.set_mode(Motor_IN2_pin, pigpio.OUTPUT)
        pi.set_mode(Motor_PWM_pin, pigpio.OUTPUT)

#Configure DC motor output(設定直流馬達輸出)    
    def power(self, power):
        if power == 0:
            pi.write(Motor_IN1_pin, pigpio.LOW)
            pi.write(Motor_IN2_pin, pigpio.LOW)
            pi.set_PWM_dutycycle(Motor_PWM_pin, 0)
        elif power > 0:
            if reverse == True:
                pi.write(Motor_IN1_pin, pigpio.LOW)
                pi.write(Motor_IN2_pin, pigpio.HIGH)
            else:
                pi.write(Motor_IN1_pin, pigpio.HIGH)
                pi.write(Motor_IN2_pin, pigpio.LOW)
            pi.set_PWM_dutycycle(Motor_PWM_pin, constrain(mapping(power, 0, 100, 0, 255), 0, 255))
        else:
            if reverse == True:
                pi.write(Motor_IN1_pin, pigpio.HIGH)
                pi.write(Motor_IN2_pin, pigpio.LOW)
            else:
                pi.write(Motor_IN1_pin, pigpio.LOW)
                pi.write(Motor_IN2_pin, pigpio.HIGH)
            value = mapping(abs(power), 0, 100, 0, 255)
            pi.set_PWM_dutycycle(Motor_PWM_pin, constrain(mapping(abs(power), 0, 100, 0, 255), 0, 255))

#Define a class for servo motors(定義伺服馬達的類別)
class servo_motor():

#Configure servo motor GPIO angle position(設定伺服馬達GPIO角位)
    def __init__(self):
        pi.set_mode(Servo_pin, pigpio.OUTPUT)

#Set servo motor angle(設定伺服馬達角度)	
    def angle(self, turn_angle):
        turn_angle = constrain(turn_angle, -servo_range, servo_range ) * -1
        self.servoangle = turn_angle + 90 + servo_offset
        duty = constrain(mapping(self.servoangle, 0, 180, 500, 2500), 500, 2500)
        pi.set_servo_pulsewidth(Servo_pin, duty)

   def _cbf(self, gpio, level, tick):
      if gpio == trigger_pin:
         if level == 0: # trigger sent
            self._triggered = True
            self._high = None
      else:
         if self._triggered:
            if level == 1:
               self._high = tick
            else:
               if self._high is not None:
                  self._time = tick - self._high
                  self._high = None
                  self._ping = True
   def read(self):
      if self._inited:
         self._ping = False
         pi.gpio_trigger(trigger_pin)
         start = time.time()
         while not self._ping:
            if (time.time()-start) > 5.0:
               return 20000
            time.sleep(0.001)
         return self._time/58.2
      else:
         return None
   def cancel(self):
      if self._inited:
         self._inited = False
         self._cb.cancel()
         pi.set_mode(trigger_pin, self._trig_mode)
         pi.set_mode(echo_pin, self._echo_mode)
		self.setMode(mode)
		time.sleep(0.02)
		return True

	def raw(self):
		return self.getVector(self.VECTOR_EULER)[0]
		
#Define a class for LiDAR(定義光達的類別)
class lidarSensor():
    def __init__(self, lidar_type):
        if lidar_type == 'D100':
            self.D100_initialization()
        self.Lidar_left = -1
        self.Lidar_right = -1
        self.Lidar_mid = -1

    def D100_initialization(self):
        rospy.init_node('listener', anonymous=True)
        rospy.Subscriber("/scan", LaserScan, self.D100_lidar_callback)

    def D100_lidar_callback(self, data):
        lens = int((data.angle_max - data.angle_min) / data.angle_increment)
        for i in range(lens):
            angle_error = int((data.angle_min + i * data.angle_increment) * RADIAN_TO_DEGREES) - 360
            if angle_error >= 0:
                angle = angle_error % 360 - 180
            else:
                angle = 359 - (-1 - angle_error) % 360 - 180
            ranges = data.ranges[i] * 100
            if not math.isnan(ranges):
                if angle > -5 and angle < 5:
                    self.Lidar_mid = round(data.ranges[i] * 100)
                if angle > 85 and angle < 95:
                    self.Lidar_left = round(data.ranges[i] * 100)
                if angle > -95 and angle < -85:
                    self.Lidar_right = round(data.ranges[i] * 100)
         
class tools():        
    def constrain(self, x, out_min, out_max):
        return out_min if x < out_min else out_max if x > out_max else x                

if __name__ == "__main__":
    print("error")

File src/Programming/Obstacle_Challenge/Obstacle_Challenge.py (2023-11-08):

# -*- coding: UTF-8 -*-
#Import the required modules(匯入所需的模組)
from vehicle_function import*

#opencv_detect.get_program_fps()  Obtaining Image Recognition FPS(取得影像辨識FPS)
#opencv_detect.get_keyboard()     Get keyboard input(取得鍵盤的按鍵)
#opencv_detect.get_green_x()      Get the X coordinate of the green block(取得綠色積木X座標)
#opencv_detect.get_green_y        Get the Y coordinate of the green block(取得綠色積木Y座標)
#opencv_detect.get_green_area()   Obtain the area size of the green block(取得綠色積木面積大小)
#opencv_detect.get_red_x()        Get the X coordinate of the red block(取得紅色積木X座標)
#opencv_detect.get_red_y          Get the Y coordinate of the red block(取得紅色積木Y座標)
#opencv_detect.get_red_area()     Obtain the area size of the red block(取得紅色積木面積大小)

#Controlling LED using methods and properties defined in the LED_control class(使用LED_control類別內部定義的方法和屬性，控制LED)
LED = LED_control()

#Reading button using methods and properties defined in the button_control class(使用button_control類別內部定義的方法和屬性，讀取按鈕)
button = button_control()

#Controlling DC motor using methods and properties defined in the dc_motor class(使用dc_motor類別內部定義的方法和屬性，控制直流馬達)
motor = dc_motor()

#Controlling servo motor using methods and properties defined in the servo_motor class(使用servo_motor類別內部定義的方法和屬性，控制伺服馬達)
servo = servo_motor()

#Reading a color sensor using methods and properties defined in the TCS34725 class(使用TCS34725類別內部定義的方法和屬性，讀取顏色感測器)
color_sensor = TCS34725()

#Using methods and properties defined in the tools class(使用tools類別內部定義的方法和屬性)
mapping = tools()

#全域變數定義(不更動)
RADIAN_TO_DEGREES = 180000/3141.59
lidar_data = 0
lidar_run = False
thread_run = True
thread_DC = True
green_lower = 0
green_upper = 0
red_lower = 0
red_upper = 0
line_middle = 0
turn_left_dis = -1
turn_right_dis = -1
servo_control_angle = 0
record_block = 'None'
direction = 'None'
return_block_color = 'None'
start_pleace = 0

#參數調整(調整參數)
dodgeblock_kp = 0.18
center_kp = 0.8
max_power = 60
min_power = 55

def handler(signum, frame):
    exit(0)

#Activate the LiDAR(啟動lidar)
def lidar_callback(data):
    global lidar_data, lidar_run
    lidar_data = data
    lidar_run = True

#Read LiDAR distances from the left, right, and front(讀取光達左測、右測、前方距離)
def lidar_get_distance(set):
    lens = int((lidar_data.angle_max - lidar_data.angle_min) / lidar_data.angle_increment) - 15
    mid = -1
    left = -1
    right = -1
    for i in range(lens):
        angle_error = int((lidar_data.angle_min + i * lidar_data.angle_increment) * RADIAN_TO_DEGREES) + 180
        if angle_error >= 0:
            angle = angle_error % 360 - 180
        else:
            angle = 359 - (-1 - angle_error) % 360 - 180
        ranges = lidar_data.ranges[i] * 100
        if ranges < 100:
            if abs(angle + i) < 5:
                #Lidar front distance value(光達前方數值)
                mid = ranges
            if abs(angle - 90 + i) < 5:
                #LiDAR left-side value(光達左邊數值)
                left = ranges
            if abs(angle + 90 + i) < 5:
                #LiDAR right-side value(光達右邊數值)
                right = ranges
    return int(left), int(mid), int(right) ,i

#Read values of the blue line and orange line(讀取藍線與橘線數值)
def line_color_read():
    global line_middle, color_direction_middle, white_color
    with open('/home/pi/Desktop/final/save_file/color_sensor.p', mode='rb') as f:
        file = pickle.load(f)
    blue_color = file['Blue']
    orange_color = file['Orange']
    white_color = file['white']
    color_direction_middle = (blue_color + orange_color) / 2 
    line_middle = (white_color + orange_color) / 2
    print('\norange:' + str(orange_color))
    print('blue:' + str(blue_color))
    print('white:' + str(white_color))
    print('\ndirection_middle:', color_direction_middle)
    print('line middle:', line_middle)
    
#Read obstacle HSV values(讀取障礙物HSV數值)
def block_color_read():
    global green_lower, green_upper, red_lower, red_upper
    with open('save_file/HSV_Green.p', mode='rb') as f:
        file = pickle.load(f)
    g_lower = file['Lower']
    g_upper = file['Upper']
    print('\nGreen_Lower:' + str(g_lower))
    print('Green_Upper:' + str(g_upper))
    with open('save_file/HSV_Red.p', mode='rb') as f:
        file = pickle.load(f)
    r_lower = file['Lower']
    r_upper = file['Upper']
    print('\nRed_Lower:' + str(r_lower))
    print('Red_Upper:' + str(r_upper) + '\n')
    
    red_lower = np.array(r_lower, np.uint8) 
    red_upper = np.array(r_upper, np.uint8)
    green_lower = np.array(g_lower, np.uint8)
    green_upper = np.array(g_upper, np.uint8)

#Read the values of the color sensor(讀取顏色感測器數值)
def color_read():
    global color
    while thread_run:
        color = color_sensor.readluminance()['c']
        time.sleep(0.01)

#=======================任務執行程序=======================

#Recognize Clockwise and Counterclockwise(辨識順逆時針)
def start_to_NoWall():
    global gyro_offset, turn_direction, reverse_direction, direction
    left_dis=50
    right_dis=50
    while left_dis < 200 and right_dis < 200:
        left_dis, right_dis, gyro_angle = dodge_control(0)
    print('left:', left_dis, ' right:', right_dis, '\n')

    #判斷順時針或逆時針
    if left_dis > right_dis:
        #逆時針
        print('turn left\n')
        direction = 'counterclockwise'
        gyro_offset = 0 #陀螺儀微調
        #正旋轉方向
        turn_direction = [-90, -180, -270, 0, 
                          -90, -180, -270, 0, 
                          -90, -180, -270
                          ]
        #反轉旋轉方向
        reverse_direction = [180, -90, 0, 90]
    else:
        #順時針
        print('turn right\n')
        direction = 'clockwise'
        gyro_offset = 0 #陀螺儀微調
        #正旋轉方向
        turn_direction = [90, 180, 270, 0,
                          90, 180, 270, 0,
                          90, 180, 270
                          ]
        #反轉旋轉方向
        reverse_direction = [180, 90, 0, -90]

#Avoid obstacles until the field line is detected(閃避障礙物直到測到場地線)
def dodge_to_line(set_gyro):
    while color > line_middle:
        left_dis, right_dis, gyro_angle = dodge_control(set_gyro)
    print(color)

#Translation in English: Avoid obstacles until the time is up(閃避障礙物直到時間到)
def dodge_to_time(set_gyro, set_time):
    reset = time.time()
    while time.time() - reset < set_time:
        left_dis, right_dis, gyro_angle = turn_dodge_control(set_gyro)
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

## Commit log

2023-08-05 工作日誌
2023-08-05 Obstacle Challenge Code overview(任務賽程式概述)
2023-08-05 Open Challenge Code overview(資格賽程式概述)
2023-08-05 Software Platform Construction(軟體平台建置)
2023-08-05 修改過的目錄
2023-08-06 add special program(特色程式)
2023-08-29 add lidar
2023-08-29 add 3D print
2023-08-29 Gear Differential
2023-08-29 3D printed product
2023-09-03 structural schematic diagram
2023-09-03 ＮoMachine
2023-09-03 add steering_overview
2023-09-09 3D Printed
2023-09-09 update camera
2023-09-10 update power supply system
2023-09-16 add Explanation of Circuit Principles
2023-09-16 add raspberry pi
2023-09-16 add flow chart of sensor
2023-09-24 Motor Selection
2023-09-29 [Raspberry Pi 4B]
2023-10-14 Vehicle Chassis Design
